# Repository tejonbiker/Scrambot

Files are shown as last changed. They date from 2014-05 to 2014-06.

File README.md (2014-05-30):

Scrambot
========

29/May/2014

University of Guanajuato

Division de Ingenierias Campus Irapuato Salamanca (DICIS)

Jose Federico Ramos Ortega

Scrambot is a differential mobile robot controlled via WiFi based
on a beetle robot from Steren as chassis and a Raspberry Pi as core of the controller.

This project begins with the ASME SPDC contest in 2013: "Remote Inspection Device":

https://www.asme.org/events/competitions/student-design-competition

The targets and the rules were quite simple:

    -The robot operator cannot see the stage
    -The robot need to establish (in any way) a real time video with the operator
    -The robot need to be controlled wirelessly
    -The robot need to accomplish three tasks:
      1.-Read a label with four numbers
      2.-Carry a small wood cylinder
      3.-Push a button 
          
The best balance between cost and flexibility was the Raspberry Pi with a lot of add-ons.
The result of the contest was this project (with a more little post work), this repo have the intention
to be a source of knowledge and contact that you require if you want to reconstruct/improve this project. 

Some topics/knowledge used in this robot are:

    -Remote connections
      -SSH
      -VNC
      -TCP sockets for server and client (ANSIC C and Java respectively)
      -MJPEG Server
      
    -Java Desktop GUI
      -Sockets
      -MJPEG Capture and show
      
    -PCB Design (with Eagle)
      -5V Switched Mode Power Suypply
      -Raspberry Pi GPIO and two L293 H-Bridge interface
      
    -Raspberry Pi GPIO management
      -WiringPi
      -I2C (for MPU6050 acelerometter)
      
    -Power Management 
      -Knowledge about batteries (NiCd - Lipo)
      -5V SMPS design
      -Power consumption analysis
      
    -Linux stuff
      -SSH and console commands management
      -Bash scripting
        -Automatically start services
        -Automatically install software
      -Make for compilation in ANSI C
      
    -Wireless LAN magagement
      -Detecting the Scrambot in LAN
      -Scrambot as hotspot
  
(Breathe.......) and much more.

For any misspelling/correction/comment/idea don't doubt to contact me.

tejonbiker@gmail.com

We will be happy if you like the project. 

Don't forget this is a MIT licensed project.

Have fun!!!!! :D

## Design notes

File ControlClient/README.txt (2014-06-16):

Scrambot Control Client

This is a desktop Java Application build on Netbeans, uses the GUI of the netbeans,
this means you only can compile with Netbeans.

The basics actions of the GUI are:
		-Open a socket connection to transfer control commands
		-Open a stream to capture the MJPEG from Scrambot
		-Capture the press/release keys 
		-Search the Scrambot in a range of IP

The application is entirely crossplatform, can be used (and develop) in any
OS that support Netbeans, currently I only tested in Linux/Win/Mac.

The executable is dist/ControlClient.jar

I highly recommend start with the file ControlGUI.java if you want inspect the code.

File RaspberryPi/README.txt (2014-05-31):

This folder includes all software related to the Raspbery Pi, as you can see the
is not much as you can think, the most large file is ScramConfig.sh
this script configures a Raspian OS to install all features of the Scrambot
and be recognized by GUI ControlClient.

The main problem is the MJPEG source, this code have some changes that need to be uptaed
in the script.

If you are in Windows please open or edit this files with CodeBlocks or some similar
IDE that recognizes Linux end lines, Visual Studio rewrites this to windows end lines.

server3.c uses WiringPi to acces to the Raspberry Pi GPIO, aditionally provides the service
(via sockets) that ControlClient uses to transfer the control commands, all is maded in ANSI C.

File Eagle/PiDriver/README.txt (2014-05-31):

PiDrive
This board designed to interface four motors with complete H-bridge, 
this task is accomplished with two L293 IC, some other sutff is addded,
like a PIC (MCU) to monitor the input voltage for the motors, the PIC is
not tested yet.

The board don't integrate a regulador to feed the Raspberry Pi with the
battery of the motors, this board only connect the battery for the motors.

The MPU6050 pinout works perfect.

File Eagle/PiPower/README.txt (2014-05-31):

PiPower
This board is designed to regulate 5V from 7V-15V battery
 voltage with an efficient  Switched Mode Power Supply, 
the board integrate an USB Female A conector to use a 
micro usb cable to power the pi, as is usual.

See more at datasheet of: LM2596

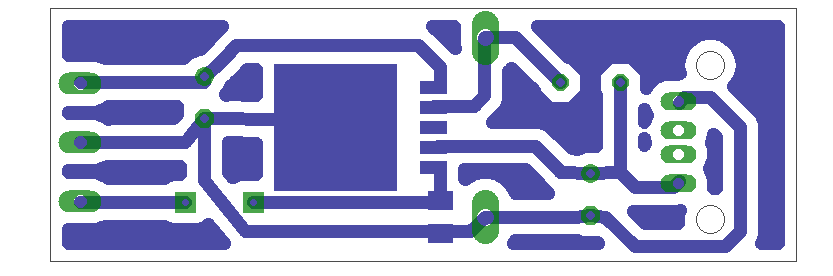
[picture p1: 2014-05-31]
Eagle/PiPower/PiPower_brd.png

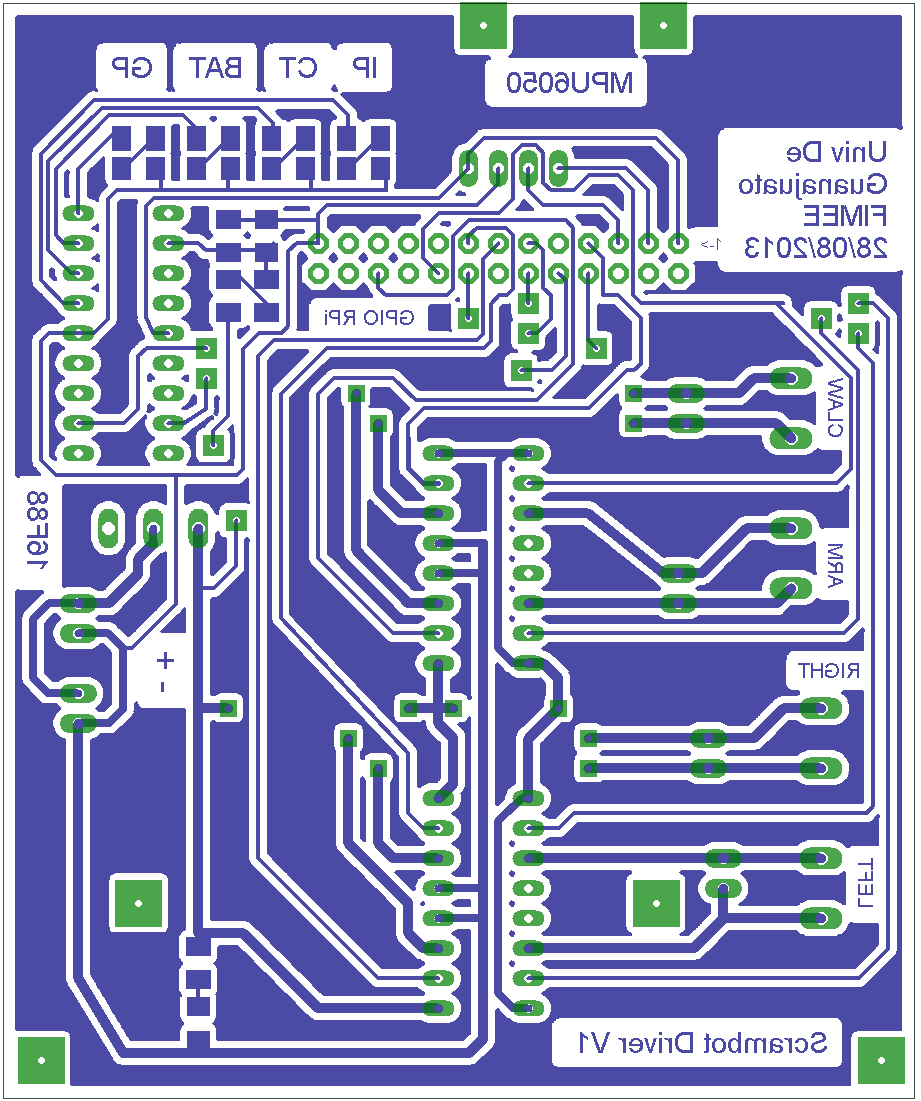
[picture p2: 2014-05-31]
Eagle/PiDriver/PiDrive_brd.png

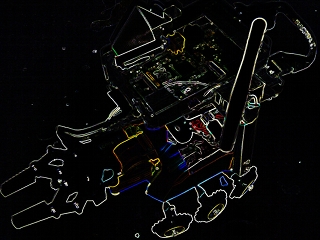
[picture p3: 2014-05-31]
ControlClient/src/blackscram.jpg

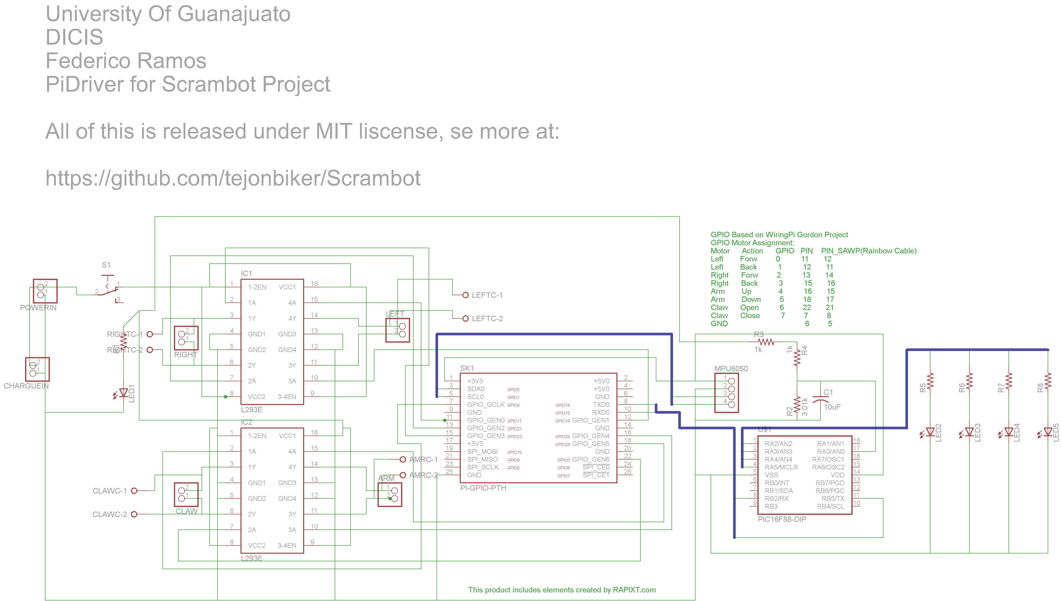
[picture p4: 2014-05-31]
Eagle/PiDriver/PiDriver_sch.png

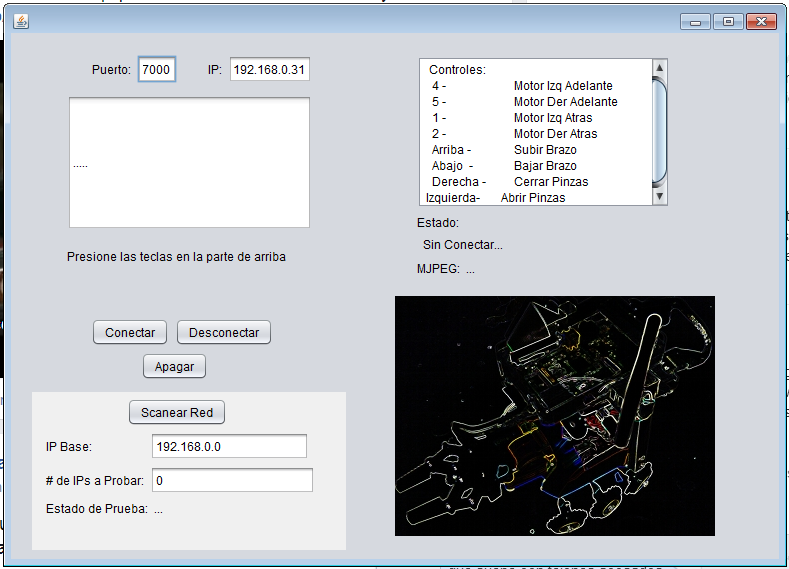
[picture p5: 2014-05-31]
ControlClient/capture_screen.png

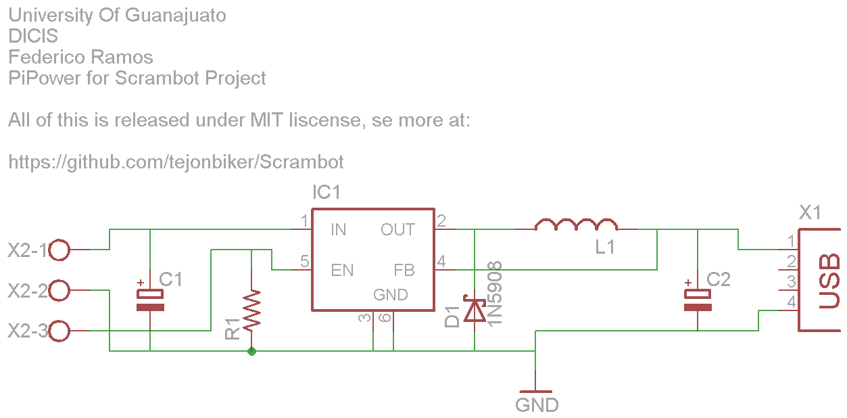
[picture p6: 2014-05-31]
Eagle/PiPower/PiPower_sch.png

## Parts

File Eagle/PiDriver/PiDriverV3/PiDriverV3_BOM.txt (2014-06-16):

Partlist exported from C:/GitHub/Scrambot/Eagle/PiDriver/PiDriverV3/PiDriverV3.sch at 08/06/2014 11:17:48 p.m.

Part      Value        Device       Package        Description                     MF                MPN   OC_FARNELL OC_NEWARK
AMRC                   W237-02P     W237-132       WAGO SREW CLAMP                                         unknown    unknown  
ARM                    PINHD-1X2    1X02           PIN HEADER                                                                  
C1        10uF         C-USC1206    C1206          CAPACITOR, American symbol                                                  
CHARGUEIN              PINHD-1X2    1X02           PIN HEADER                                                                  
CLAW                   PINHD-1X2    1X02           PIN HEADER                                                                  
CLAWC                  W237-02P     W237-132       WAGO SREW CLAMP                                         unknown    unknown  
D1        1N5819-T     1N5819-T     DO41-7.6       1.0A SCHOTTKY BARRIER RECTIFIER                                             
D2        1N5819-T     1N5819-T     DO41-7.6       1.0A SCHOTTKY BARRIER RECTIFIER                                             
D3        1N5819-T     1N5819-T     DO41-7.6       1.0A SCHOTTKY BARRIER RECTIFIER                                             
D4        1N5819-T     1N5819-T     DO41-7.6       1.0A SCHOTTKY BARRIER RECTIFIER                                             
D5        1N5819-T     1N5819-T     DO41-7.6       1.0A SCHOTTKY BARRIER RECTIFIER                                             
D6        1N5819-T     1N5819-T     DO41-7.6       1.0A SCHOTTKY BARRIER RECTIFIER                                             
D7        1N5819-T     1N5819-T     DO41-7.6       1.0A SCHOTTKY BARRIER RECTIFIER                                             
D8        1N5819-T     1N5819-T     DO41-7.6       1.0A SCHOTTKY BARRIER RECTIFIER                                             
D9        1N5819-T     1N5819-T     DO41-7.6       1.0A SCHOTTKY BARRIER RECTIFIER                                             
D10       1N5819-T     1N5819-T     DO41-7.6       1.0A SCHOTTKY BARRIER RECTIFIER                                             
D11       1N5819-T     1N5819-T     DO41-7.6       1.0A SCHOTTKY BARRIER RECTIFIER                                             
D12       1N5819-T     1N5819-T     DO41-7.6       1.0A SCHOTTKY BARRIER RECTIFIER                                             
D13       1N5819-T     1N5819-T     DO41-7.6       1.0A SCHOTTKY BARRIER RECTIFIER                                             
D14       1N5819-T     1N5819-T     DO41-7.6       1.0A SCHOTTKY BARRIER RECTIFIER                                             
D15       1N5819-T     1N5819-T     DO41-7.6       1.0A SCHOTTKY BARRIER RECTIFIER                                             
D16       1N5819-T     1N5819-T     DO41-7.6       1.0A SCHOTTKY BARRIER RECTIFIER                                             
IC1       L293E        L293E        DIL16          TI DEVICE                       Arrow Electronics L293E 1467711    89K0732  
IC2       L293E        L293E        DIL16          TI DEVICE                       Arrow Electronics L293E 1467711    89K0732  
LED1                   LEDSMT1206   1206           LED                                                                         
LED2                   LEDSMT1206   1206           LED                                                                         
LED3                   LEDSMT1206   1206           LED                                                                         
LED4                   LEDSMT1206   1206           LED                                                                         
LED5                   LEDSMT1206   1206           LED                                                                         
LEFT                   PINHD-1X2    1X02           PIN HEADER                                                                  
LEFTC                  W237-02P     W237-132       WAGO SREW CLAMP                                         unknown    unknown  
MPU6050                PINHD-1X4    1X04           PIN HEADER                                                                  
POWERIN                PINHD-1X2    1X02           PIN HEADER                                                                  
R1                     R-US_M1206   M1206          RESISTOR, American symbol                                                   
R2        3.01k        R-US_M1206   M1206          RESISTOR, American symbol                                                   
R3        1k           R-US_M1206   M1206          RESISTOR, American symbol                                                   
R4        1k           R-US_M1206   M1206          RESISTOR, American symbol                                                   
R5                     R-US_M1206   M1206          RESISTOR, American symbol                                                   
R6                     R-US_M1206   M1206          RESISTOR, American symbol                                                   
R7                     R-US_M1206   M1206          RESISTOR, American symbol                                                   
R8                     R-US_M1206   M1206          RESISTOR, American symbol                                                   
RIGHT                  PINHD-1X2    1X02           PIN HEADER                                                                  
RIGHTC                 W237-02P     W237-132       WAGO SREW CLAMP                                         unknown    unknown  
S1                     255SB        255SB          SLIDING SWITCH                                                              
SK1       PI-GPIO-PTH  PI-GPIO-PTH  GPIO-CONNECTOR Raspberry Pi                                                                
SMPS                   PINHD-1X2    1X02           PIN HEADER                                                                  
U$1       PIC16F88-DIP PIC16F88-DIP DIL18          8-bit PIC uC

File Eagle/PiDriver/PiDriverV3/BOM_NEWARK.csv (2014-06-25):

N.º de artículo | No. Parte Newark | ¿Conforme a RoHS? | Notas | Cantidad | Número Parte Fabricante | Fabricante / Descripción | Disponibilidad | Precio unitario | Total de línea | Precio de descuento
1 | 41K4141 | YES |  | 1.0 | LM2675M-5.0/NOPB | TEXAS INSTRUMENTS IC, STEP-DOWN REGULATOR, SOIC-8 TEXAS INSTRUMENTS-LM2675M-5.0/NOPB-IC, STEP-DOWN REGULATOR, SOIC-8 | 5500 | 5.97 | 5.97
2 | 68R4966 | YES |  | 2.0 | CC1206KRX7R9BB103 | YAGEO CAPACITOR CERAMIC 0.01UF, 50V, X7R, 10%, 1206 YAGEO-CC1206KRX7R9BB103-CAPACITOR CERAMIC 0.01UF, 50V, X7R, 10%, 1206 | 5460 | 0.05 | 0.10
3 | 46P8758 | YES |  | 1.0 | 13R473C | MURATA POWER SOLUTIONS INDUCTOR, 47UH, 1.5A, RADIAL LEADED MURATA POWER SOLUTIONS-13R473C-INDUCTOR, 47UH, 1.5A, RADIAL LEADED | 329 (Disponible hasta que se agoten las existencias) | 0.85 | 0.85
4 | 16M7370 | YES |  | 1.0 | EKZE160ELL680MF07D | UNITED CHEMI-CON CAPACITOR ALUM ELEC 68UF, 16V, 20%, RADIAL UNITED CHEMI-CON-EKZE160ELL680MF07D-CAPACITOR ALUM ELEC 68UF, 16V, 20%, RADIAL | 728 | 0.38 | 0.38
5 | 38K4678 | YES |  | 1.0 | MCGPR25V107M6.3X11 | MULTICOMP CAPACITOR ALUM ELEC 100UF, 25V, 20%, RADIAL MULTICOMP-MCGPR25V107M6.3X11-CAPACITOR ALUM ELEC 100UF, 25V, 20%, RADIAL | 3638 | 0.14 | 0.14
6 | 05R5876 | YES |  | 1.0 | SSA23L-E3/61T | VISHAY GENERAL SEMICONDUCTOR SCHOTTKY RECTIFIER, 2A 30V DO-214AC VISHAY GENERAL SEMICONDUCTOR-SSA23L-E3/61T-SCHOTTKY RECTIFIER, 2A 30V DO-214AC | 952 | 0.31 | 0.31
7 | 90R9531 | Y-EX |  | 16.0 | 1N5819 | MULTICOMP SCHOTTKY DIODE, 1A, 40V, DO-41 MULTICOMP-1N5819-SCHOTTKY DIODE, 1A, 40V, DO-41 | 5056 | 0.08 | 1.31
8 | 08F8145 | YES |  | 2.0 | SN754410NE | TEXAS INSTRUMENTS IC, PERIPHERAL DRIVER, HALF-H, 1A, DIP16 TEXAS INSTRUMENTS-SN754410NE-IC, PERIPHERAL DRIVER, HALF-H, 1A, DIP16 | 71 | 3.38 | 6.76
9 | 70R0063 | YES |  | 4.0 | PT1 | 5/2-5.0-H | PHOENIX CONTACT TERM BLOCK, PCB, SCREW, 5.0MM, 2WAY PHOENIX CONTACT-PT1,5/2-5.0-H-TERM BLOCK, PCB, SCREW, 5.0MM, 2WAY | 3468 | 0.50 | 1.98
10 | 54K2830 | YES |  | 1.0 | PIC16F88-I/P | MICROCHIP MCU, 8BIT, PIC16, 20MHZ, DIP-18 MICROCHIP-PIC16F88-I/P-MCU, 8BIT, PIC16, 20MHZ, DIP-18 | 1332 | 3.39 | 3.39
11 | 89M6854 | YES |  | 1.0 | CRCW12062K61FKEA | VISHAY DALE RESISTOR, THICK FILM, 2.61KOHM, 250mW, 1% VISHAY DALE-CRCW12062K61FKEA-RESISTOR, THICK FILM, 2.61KOHM, 250mW, 1% | 3571 | 0.14 | 0.14
12 | 53K2402 | Y-EX |  | 1.0 | CRCW1206422RFKEA | VISHAY DALE RESISTOR, THICK FILM, 422 OHM, 250mW, 1% VISHAY DALE-CRCW1206422RFKEA-RESISTOR, THICK FILM, 422 OHM, 250mW, 1% | 2743 | 0.01 | 0.01
13 | 75R5071 | YES |  | 1.0 | BZV55-C3V3 | 115 | NXP ZENER DIODE, 500mW, 3.3V, SOD-80C NXP-BZV55-C3V3,115-ZENER DIODE, 500mW, 3.3V, SOD-80C | 2368 | 0.03 | 0.03
14 | 70K9170 | YES |  | 1.0 | C1206C106K4RACTU | KEMET CAPACITOR CERAMIC, 10UF, 16V, X7R, 10%, 1206 KEMET-C1206C106K4RACTU-CAPACITOR CERAMIC, 10UF, 16V, X7R, 10%, 1206 | 2770 | 0.54 | 0.54
15 | 93K6506 | YES |  | 1.0 | CMD15-21VRD/TR8 | CHICAGO MINIATURE LIGHTING LED, RED, 1.5MM X 2MM, 4MCD, 640NM CHICAGO MINIATURE LIGHTING-CMD15-21VRD/TR8-LED, RED, 1.5MM X 2MM, 4MCD, 640NM | 3703 | 0.27 | 0.27
16 | 15M8857 | YES |  | 2.0 | CMD15-21VGC/TR8 | CHICAGO MINIATURE LIGHTING LED, GREEN, 1.5MM X 2MM, 10MCD, 570NM CHICAGO MINIATURE LIGHTING-CMD15-21VGC/TR8-LED, GREEN, 1.5MM X 2MM, 10MCD, 570NM | 2277 | 0.28 | 0.56
17 | 93K6508 | YES |  | 2.0 | CMD15-21VYD/TR8 | CHICAGO MINIATURE LIGHTING LED, YELLOW, 1.5MM X 2MM, 4MCD, 585NM CHICAGO MINIATURE LIGHTING-CMD15-21VYD/TR8-LED, YELLOW, 1.5MM X 2MM, 4MCD, 585NM | 962 | 0.27 | 0.54
18 | 79M6160 | YES |  | 1.0 | MC1206S4F2200T5E | MULTICOMP RESISTOR, THICK FILM, 220 OHM, 250mW, 1% MULTICOMP-MC1206S4F2200T5E-RESISTOR, THICK FILM, 220 OHM, 250mW, 1% | 1624 | 0.10 | 0.10
19 | 53K2345 | Y-EX |  | 1.0 | CRCW12064K02FKEA | VISHAY DALE RESISTOR, THICK FILM, 4.02KOHM, 250mW, 1% VISHAY DALE-CRCW12064K02FKEA-RESISTOR, THICK FILM, 4.02KOHM, 250mW, 1% | 4917 | 0.01 | 0.01
 |  |  |  |  |  |  | Subtotal | 23.40
 |  |  |  |  |  |  | Total de mercancías | 23.40
 |  |  |  |  |  |  | Envío básico | 0.00
 |  |  |  |  |  |  | Impuestos | 0.00
 |  |  |  |  |  |  | Total | 23.40

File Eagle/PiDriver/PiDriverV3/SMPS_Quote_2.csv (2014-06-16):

N.º de artículo | No. Parte Newark | ¿Conforme a RoHS? | Notas | Cantidad | Número Parte Fabricante | Fabricante / Descripción | Disponibilidad | Precio unitario | Total de línea | Precio de descuento
1 | 90W2861 | YES |  | 1.0 | MC0805B103J500CT | MULTICOMP CAP, MLCC, 10NF, 50V, X7R, 0805 MULTICOMP-MC0805B103J500CT-CAP, MLCC, 10NF, 50V, X7R, 0805 | 1569 | 0.11 | 0.11
2 | 41K4141 | YES |  | 1.0 | LM2675M-5.0/NOPB | TEXAS INSTRUMENTS IC, STEP-DOWN REGULATOR, SOIC-8 TEXAS INSTRUMENTS-LM2675M-5.0/NOPB-IC, STEP-DOWN REGULATOR, SOIC-8 | 6275 | 5.97 | 5.97
3 | 09J2996 | YES |  | 1.0 | SRU1048-470Y | BOURNS INDUCTOR, SHIELDED, 47UH, 1.5A, SMD BOURNS-SRU1048-470Y-INDUCTOR, SHIELDED, 47UH, 1.5A, SMD | Normalmente no está en inventario | 0.98 | 0.98
4 | 89K1595 | YES |  | 1.0 | STPS2150A | STMICROELECTRONICS SCHOTTKY RECTIFIER, 2A, 150V, DO-214AC STMICROELECTRONICS-STPS2150A-SCHOTTKY RECTIFIER, 2A, 150V, DO-214AC | 6639 | 0.79 | 0.79
 |  |  |  |  |  |  | Subtotal | 7.85
 |  |  |  |  |  |  | Total de mercancías | 7.85
 |  |  |  |  |  |  | Envío básico | 0.00
 |  |  |  |  |  |  | Impuestos | 0.00
 |  |  |  |  |  |  | Total | 7.85

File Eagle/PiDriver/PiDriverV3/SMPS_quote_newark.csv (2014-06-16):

N.º de artículo | No. Parte Newark | ¿Conforme a RoHS? | Notas | Cantidad | Número Parte Fabricante | Fabricante / Descripción | Disponibilidad | Precio unitario | Total de línea | Precio de descuento
1 | 04P2013 | YES |  | 3.0 | SRR1260-101M | BOURNS INDUCTOR, SHIELDED, 100UH, 1.7A, SMD BOURNS-SRR1260-101M-INDUCTOR, SHIELDED, 100UH, 1.7A, SMD | 634 | 1.31 | 3.93
2 | 53W3788 | YES |  | 6.0 | EEE-1EA101AP | PANASONIC CAPACITOR ALUM ELEC, 100UF, 25V, 20%, SMD PANASONIC-EEE-1EA101AP-CAPACITOR ALUM ELEC, 100UF, 25V, 20%, SMD | 960 | 0.70 | 4.18
3 | 65W8554 | YES |  | 3.0 | B240A-13-F | MULTICOMP DIODE, SCHOTTKY, 2A, 40V, DO-214AC-2 MULTICOMP-B240A-13-F-DIODE, SCHOTTKY, 2A, 40V, DO-214AC-2 | 1667 | 0.36 | 1.07
4 | 41K3690 | YES |  | 3.0 | LM2576S-5.0/NOPB | TEXAS INSTRUMENTS IC, STEP-DOWN VOLTAGE REGULATOR, TO-263 TEXAS INSTRUMENTS-LM2576S-5.0/NOPB-IC, STEP-DOWN VOLTAGE REGULATOR, TO-263 | 1480 | 4.42 | 13.26
 |  |  |  |  |  |  | Subtotal | 22.43
 |  |  |  |  |  |  | Total de mercancías | 22.43
 |  |  |  |  |  |  | Envío básico | 0.00
 |  |  |  |  |  |  | Impuestos | 0.00
 |  |  |  |  |  |  | Total | 22.43

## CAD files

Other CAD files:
media/ScrambotLogo.blend

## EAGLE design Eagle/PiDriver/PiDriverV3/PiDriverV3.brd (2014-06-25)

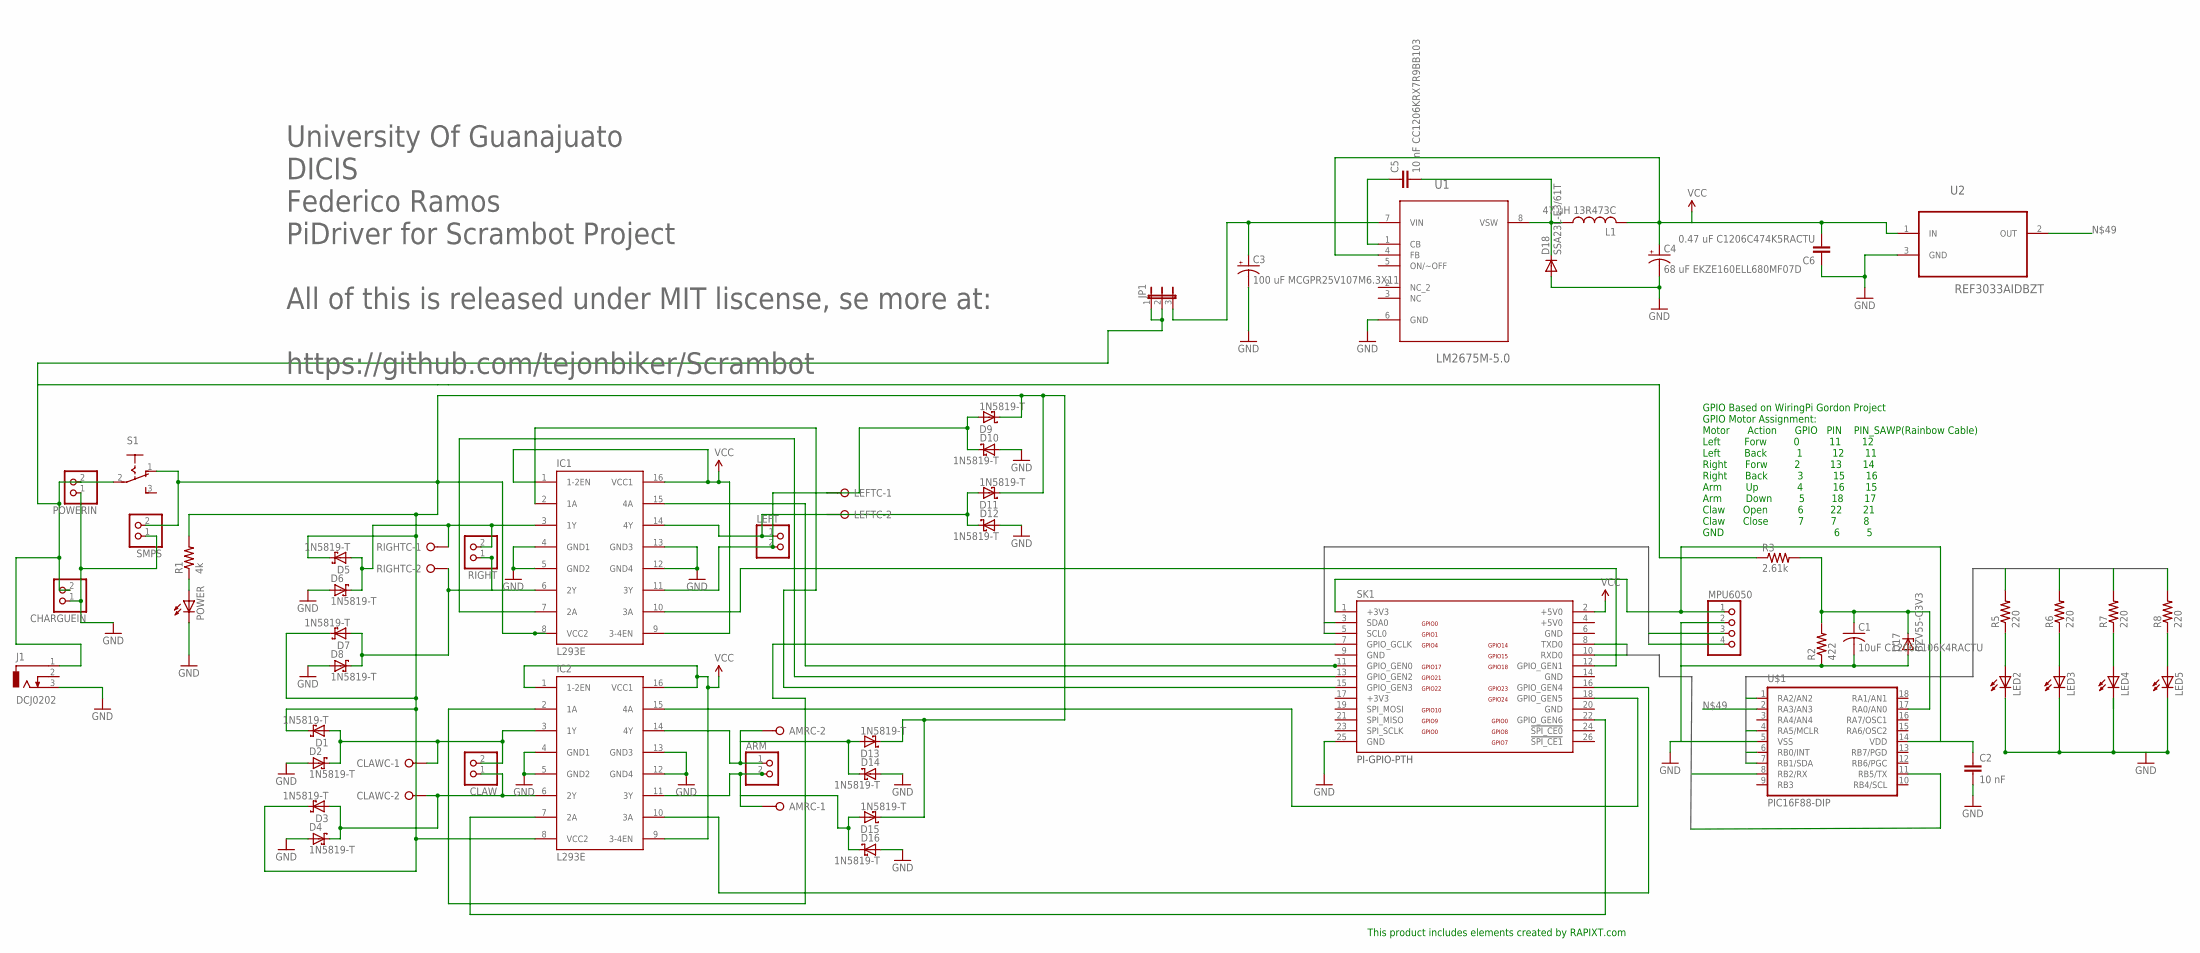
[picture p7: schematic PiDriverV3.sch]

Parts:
AMRC: W237-02P; W237-132
ARM: PINHD-1X2; 1X02
C1: 10uF C1206C106K4RACTU; C1206
C2: 10 nF; C1206
C3: 100 uF MCGPR25V107M6.3X11; E1,8-4
C4: 68 uF EKZE160ELL680MF07D; E1,8-4
C5: 10 nF CC1206KRX7R9BB103; C1206
C6: 0.47 uF C1206C474K5RACTU; C1206
CHARGUEIN: PINHD-1X2; 1X02
CLAW: PINHD-1X2; 1X02
CLAWC: W237-02P; W237-132
D1, D2, D3, D4, D5, D6, D7, D8, D9, D10, D11, D12, D13, D14, D15, D16: 1N5819-T; DO41-7.6
D17: BZV55-C3V3; SOD80C
D18: SSA23L-E3/61T; DO-214AC
IC1, IC2: L293E; DIL16
J1: DCJ0202
JP1: JP2E; JP2
L1: 47 uH 13R473C; 6000-XXXX-RC
LED2, LED3, LED4, LED5: LEDSMT1206; 1206
LEFT: PINHD-1X2; 1X02
LEFTC: W237-02P; W237-132
MPU6050: PINHD-1X4; 1X04
POWER: LEDSMT1206; 1206
POWERIN: PINHD-1X2; 1X02
R1: 4k; M1206
R2: 422; M1206
R3: 2.61k; M1206
R5, R6, R7, R8: 220; M1206
RIGHT: PINHD-1X2; 1X02
RIGHTC: W237-02P; W237-132
S1: 255SB
SK1: PI-GPIO-PTH; GPIO-CONNECTOR
SMPS: PINHD-1X2; 1X02
U1: LM2675M-5.0; SOIC127P620X175-8N
U2: REF3033AIDBZT; SOT95P237X112-3N
U$1: PIC16F88-DIP; DIL18

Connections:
+3V3: SK1.17 (+3V3)
+5V0: SK1.4 (+5V0)
ARMC: IC2.2 (1A), SK1.7 (GPIO_GCLK)
GND: C6.1, U2.3 (GND)
HTX: SK1.8 (TXD0), U$1.8 (RB2/RX)
unnamed: POWER.A, R1.1
unnamed: LED2.A, R5.1
unnamed: D9.A, D10.C, IC1.11 (3Y), LEFT.2, LEFTC.1
unnamed: IC2.10 (3A), SK1.16 (GPIO_GEN4)
unnamed: IC1.2 (1A), SK1.15 (GPIO_GEN3)
unnamed: IC1.7 (2A), SK1.13 (GPIO_GEN2)
unnamed: IC1.10 (3A), SK1.12 (GPIO_GEN1)
unnamed: D1.C, D3.C, D5.C, D7.C, D9.C, D11.C, D13.C, D15.C, IC1.8 (VCC2), IC2.8 (VCC2), R1.2, S1.1 (O), SMPS.2
unnamed: AMRC.2, ARM.1, D13.A, D14.C, IC2.14 (4Y)
unnamed: AMRC.1, ARM.2, D15.A, D16.C, IC2.11 (3Y)
unnamed: D11.A, D12.C, IC1.14 (4Y), LEFT.1, LEFTC.2
unnamed: R5.2, U$1.1 (RA2/AN2)
unnamed: C2.1, MPU6050.1, SK1.1 (+3V3), U$1.14 (VDD)
unnamed: IC2.15 (4A), SK1.18 (GPIO_GEN5)
unnamed: LED3.A, R6.1
unnamed: IC2.7 (2A), SK1.22 (GPIO_GEN6)
unnamed: SK1.10 (RXD0), U$1.11 (RB5/TX)
unnamed: CLAW.2, CLAWC.1, D1.A, D2.C, IC2.3 (1Y)
unnamed: D5.A, D6.C, IC1.3 (1Y), RIGHT.2, RIGHTC.1
unnamed: C5.2, D18.C, L1.1, U1.8 (VSW)
unnamed: IC1.15 (4A), SK1.11 (GPIO_GEN0)
unnamed: C3.+, JP1.3, U1.7 (VIN)
unnamed: C1.1, D17.C, R2.2, R3.2, U$1.17 (RA0/AN0)
unnamed: R6.2, U$1.4 (RA5/MCLR)
unnamed: LED4.A, R7.1
unnamed: CLAW.1, CLAWC.2, D3.A, D4.C, IC2.6 (2Y)
unnamed: D7.A, D8.C, IC1.6 (2Y), RIGHT.1, RIGHTC.2
unnamed: LED5.A, R8.1
unnamed: C5.1, U1.1 (CB)
unnamed: R7.2, U$1.6 (RB0/INT)
unnamed: C1.2, C2.2, C3.-, C4.-, CHARGUEIN.1, D2.A, D4.A, D6.A, D8.A, D10.A, D12.A, D14.A, D16.A, D17.A, D18.A, IC1.4 (GND1), IC1.5 (GND2), IC1.12 (GND4), IC1.13 (GND3), IC2.4 (GND1), IC2.5 (GND2), IC2.12 (GND4), IC2.13 (GND3), J1.3, LED2.C, LED3.C, LED4.C, LED5.C, MPU6050.2, POWER.C, POWERIN.1, R2.1, SK1.6 (GND), SK1.9 (GND), SK1.14 (GND), SK1.20 (GND), SK1.25 (GND), SMPS.1, U1.6 (GND), U$1.5 (VSS)
unnamed: R8.2, U$1.7 (RB1/SDA)
unnamed: U2.2 (OUT), U$1.2 (RA3/AN3)
unnamed: CHARGUEIN.2, J1.1, JP1.1, JP1.2, POWERIN.2, R3.1, S1.2
SCL: MPU6050.3, SK1.5 (SCL0)
SDA: MPU6050.4, SK1.3 (SDA0)
VCC: C4.+, C6.2, IC1.1 (1-2EN), IC1.9 (3-4EN), IC1.16 (VCC1), IC2.1 (1-2EN), IC2.9 (3-4EN), IC2.16 (VCC1), L1.2, SK1.2 (+5V0), U1.4 (FB), U2.1 (IN)

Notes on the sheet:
GPIO Based on WiringPi Gordon Project GPIO Motor Assignment: Motor Action GPIO PIN PIN_SAWP(Rainbow Cable) Left Forw 0 11 12 Left Back 1 12 11 Right Forw 2 13 14 Right Back 3 15 16 Arm Up 4 16 15 Arm Down 5 18 17 Claw Open 6 22 21 Claw Close 7 7 8 GND 6 5
This product includes elements created by RAPIXT.com
University Of Guanajuato DICIS Federico Ramos PiDriver for Scrambot Project All of this is released under MIT liscense, se more at: https://github.com/tejonbiker/Scrambot

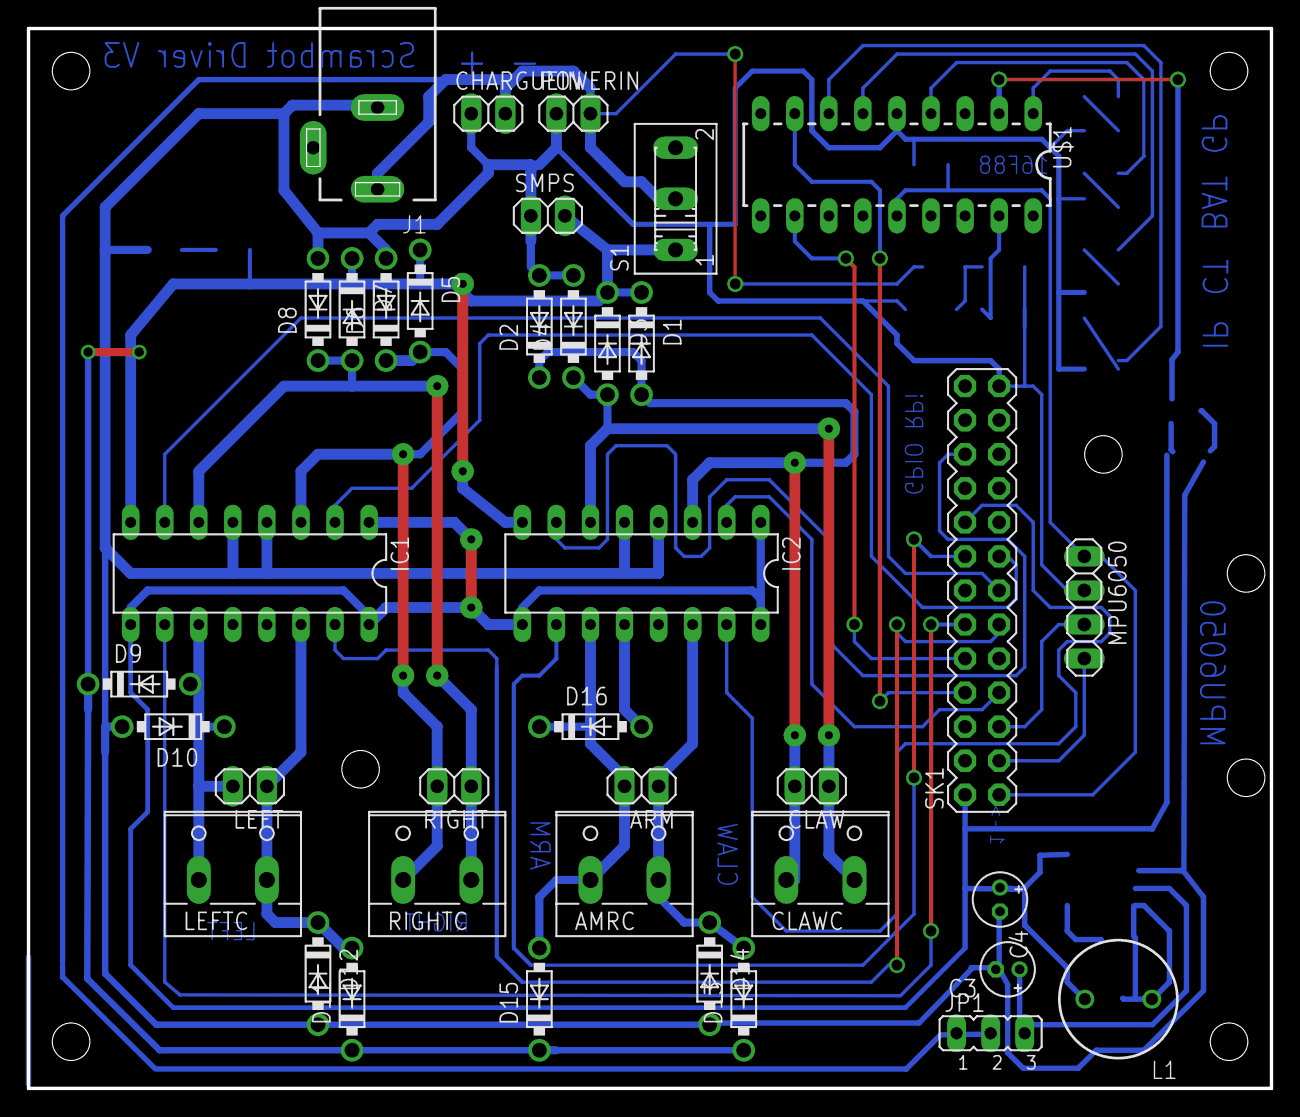
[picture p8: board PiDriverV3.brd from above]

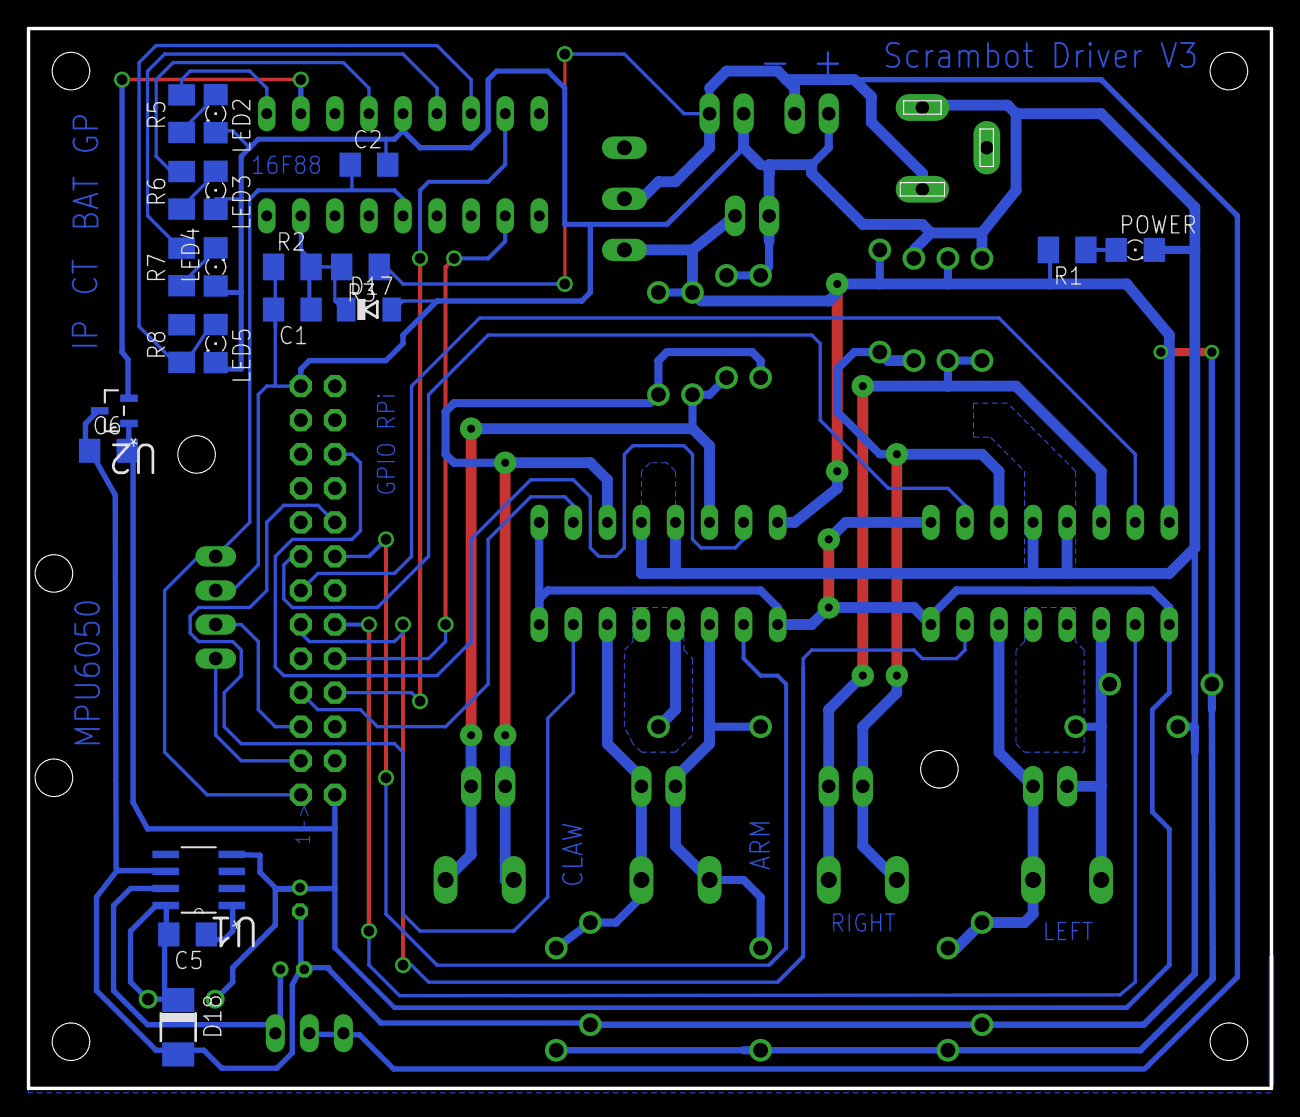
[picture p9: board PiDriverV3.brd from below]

Board: 2 copper layers, 92.7 x 79.0 mm, 58 parts (20 on the bottom side), 40 nets.

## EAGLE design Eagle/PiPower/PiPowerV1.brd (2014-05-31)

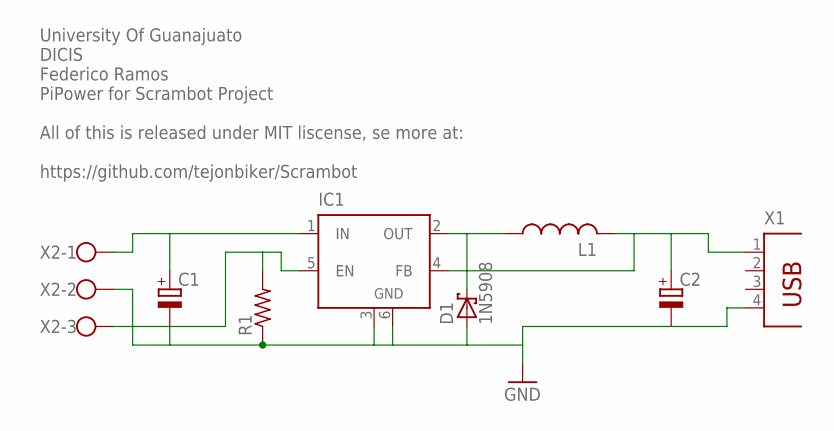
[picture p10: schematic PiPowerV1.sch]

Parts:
C1, C2: CPOL-EUE3.5-10; E3,5-10
D1: 1N5908; C4111-15
IC1: LM2596S; TO263-5
L1: L-US0204/5; 0204/5
R1: R-US_M1206; M1206
X1: PN87520
X2: W237-103

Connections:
unnamed: C2.+, IC1.4 (FB), L1.2, X1.1
unnamed: C1.+, IC1.1 (IN), X2.1
unnamed: IC1.5 (EN), R1.2, X2.3
unnamed: D1.C, IC1.2 (OUT), L1.1
unnamed: C1.-, C2.-, D1.A, IC1.3 (GND), IC1.6 (GND), R1.1, X1.4, X2.2

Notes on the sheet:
University Of Guanajuato DICIS Federico Ramos PiPower for Scrambot Project All of this is released under MIT liscense, se more at: https://github.com/tejonbiker/Scrambot

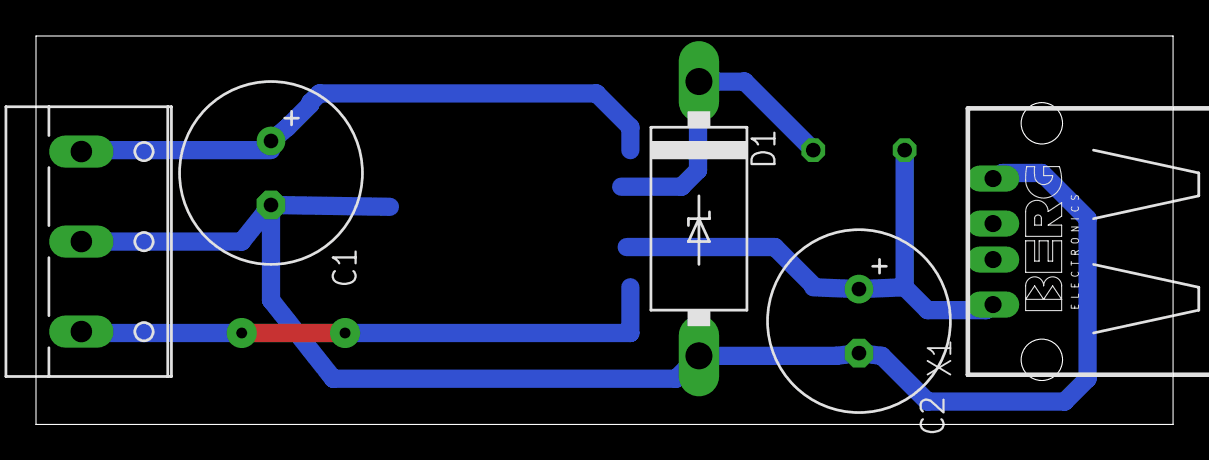
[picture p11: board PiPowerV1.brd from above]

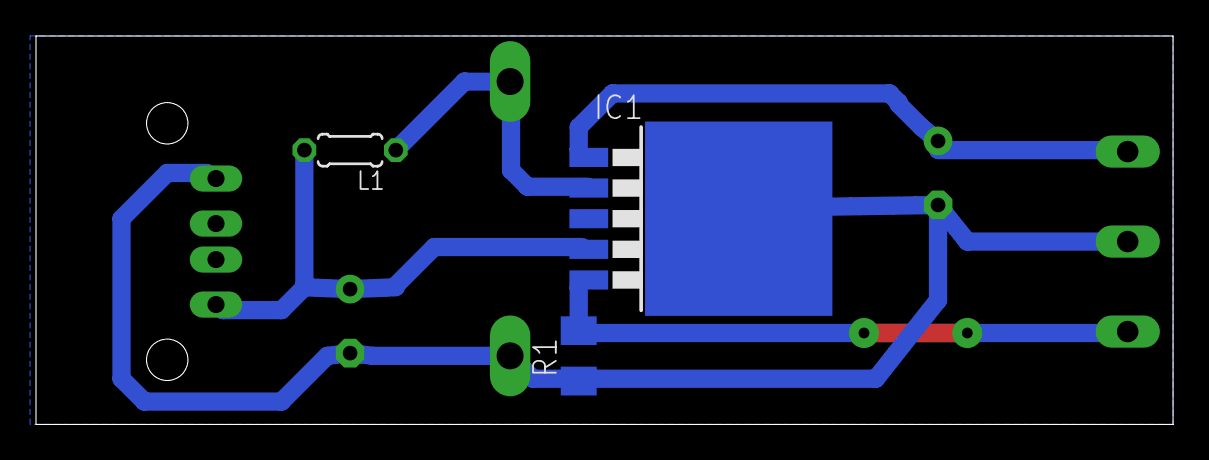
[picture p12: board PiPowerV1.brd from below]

Board: 2 copper layers, 63.2 x 21.6 mm, 8 parts (3 on the bottom side), 5 nets.

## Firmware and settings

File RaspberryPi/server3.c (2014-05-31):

/*
 * This software is part of the Scrambot project, for more info go to:
 * https://github.com/tejonbiker/Scrambot
 *
 * All source code of the project is MIT License
 *
 * This code is a modified version of:
 * http://www.linuxhowtos.org/C_C++/socket.htm
 *
 *
 * The workflow is as follow:
        Main:
                -Init WiringPi
                -Shutdown pins
                -Init Socket
                -Wait for a connection
        doStuff:
                -Send String ID
                -Read commands
                -put the commands to the GPIO
                -Wait for a command
 */

/* A simple server in the internet domain using TCP
 The port number is passed as an argument */


#include <stdio.h>
#include <stdlib.h>
#include <string.h>
#include <unistd.h>
#include <sys/types.h>
#include <sys/socket.h>
#include <netinet/in.h>

//For GPIO interface
#include <wiringPi.h>

//Flag that indicates we are in Raspberry Pi
//Added for some desktop Linux testings
#define RPI_SERVER

#define LED 0


//Debug output function
void error(const char *msg)
{
    perror(msg);
    exit(1);
}

//Function that children executes
void dostuff (int sock);

int main(int argc, char *argv[])
{
    //Paramters for socket connection
	int sockfd, newsockfd, portno;
	socklen_t clilen;
	int pid;
	char buffer[256];
	int i;
	struct sockaddr_in serv_addr, cli_addr;
	int n;

	//check for a port provided by user
	if (argc < 2) {
		fprintf(stderr,"ERROR, no port provided\n");
		exit(1);
	}

	printf("Ajustando GPIO...\n");

    //Setup WiringPi (and GPIOS)
	#ifdef RPI_SERVER
	//setup GPIO
	if(wiringPiSetup()==-1)
	{
		printf("Error al arrcancar WiringPi");
		return -2;
	}

    //Shutdown all pins, (for some reasen some pins boot)
    //with ones, until they are shutdown at this moment
	for(i=0;i<8;i++)
	{
		pinMode(i,OUTPUT);
		digitalWrite(i,0);
	}
	#endif

	printf("GPIO Listos\n");

    //let's begin with the sockets
	sockfd = socket(AF_INET, SOCK_STREAM, 0); //We want an internet socket
	if (sockfd < 0)
        error("ERROR opening socket");
	bzero((char *) &serv_addr, sizeof(serv_addr));


	portno = atoi(argv[1]);
	serv_addr.sin_family = AF_INET;         //We han a internet connection
	serv_addr.sin_addr.s_addr = INADDR_ANY;
	serv_addr.sin_port = htons(portno);     //Setup the port

	//Bind the socket to the parameters
	if (bind(sockfd, (struct sockaddr *) &serv_addr,
			 sizeof(serv_addr)) < 0)
		error("ERROR on binding");

    //only listen for 5 concurrently connections
	listen(sockfd,5);
	clilen = sizeof(cli_addr);

	while (1) {

		//Wair for a connection
		newsockfd = accept(sockfd, (struct sockaddr *) &cli_addr, &clilen);
		if (newsockfd < 0)
			error("ERROR on accept");
        //We duplicate the program, to avoid quit and kill the program
		pid = fork();
		if (pid < 0)
			error("ERROR on fork");
		if (pid == 0)  {
		    //the children excecutes the task (dostuff), the father wait for other
            //connections
			close(sockfd);
			dostuff(newsockfd);
			exit(0);
		}
		else close(newsockfd);
		printf("Cerrando Conexion\n");
	} /* end of while */
	close(sockfd);

	return 0;
}
/*For more info of how works this function see
    ControlGUI.java in ControlClient folder
*/
void dostuff (int sock)
{
	int n,m;
	char buffer[256];
	int i;

    //When a connection is stablished, the Scrambot send a string for ID
    //This is not a password!!!!
	n = write(sock,"TACOCABANA1989",14);
	n = write(sock,"1",1);

    //In reality this is an infinite loop
	while(n>0)
	{
	    //Wait for a command
		n = read(sock,buffer,255);
		//When a command is received, send a acknowledge
		m = write(sock,"OK",2);


		//Read the array and on the corresponding motor
		for(i=0;i<8;i++)
		{

			if(buffer[i]=='1')
			{
				#ifdef RPI_SERVER
				digitalWrite(i,1);
				#endif
			}
			else if(buffer[i]==216)
			{
			    //if the program send a special character in
			    //any slot, we shutdown the Raspberry Pi
			    printf("Apagando...");
			    system("sudo halt");
			    exit(0);
			}
			else
			{

				#ifdef RPI_SERVER
				digitalWrite(i,0);
				#endif
			}
		}

        //Clean un the buffer, to avoid fake readings
		buffer[8]=0;
	    //    printf("%s \n",buffer);
		//printf("%i\n",n);
	}

}

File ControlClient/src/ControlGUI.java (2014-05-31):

/*
 * This software is part of the Scrambot project, for more info go to:
 * https://github.com/tejonbiker/Scrambot
 * 
 * All source code of the project is MIT License
 * 
 * The workflow is as follow:
 *      ControlGUI()
 *          PiClient()
 *          MJPEGViewer()
 * 
 * From here the GUI events takes the control
 * 
 *      keypressed/keyReleased: control command user input (socket transfer via
 *                              PiClient)
 *      actionPerformed: Botton actions
 *              -Conectar: Open the sockets with the text on IP Jlabel,
 *                         Aditionaly init the MJPEG capture
 *              -Desconectar: close all connections
 *              -Apagar: Sends a special character to the server in
 *                       Scrambot that shutdown the Raspberry Pi
 *              -Scanear Red: Init the scanIPRange function
 * 
 *       scanIPRange: based on the values of the textbox "IP Base" and 
 *                  "# de IPs a Probar" scan a range of IP for the scrambot
 *                  and perform a full connection behavior if the scrambot
 *                  is found
 */
import java.awt.*;
import java.awt.event.ActionEvent;
import java.awt.event.ActionListener;
import java.awt.event.KeyEvent;
import java.awt.event.KeyListener;
import java.io.IOException;
import java.net.*;
import java.util.logging.Level;
import java.util.logging.Logger;
import javax.swing.*;

/*
 * To change this template, choose Tools | Templates
 * and open the template in the editor.
 */

/**
 *
 * @author Tejon
 */
public class ControlGUI extends javax.swing.JFrame implements KeyListener, ActionListener {

    /**
     * Creates new form ControlGUI
     */
    
    //Number of max transfered bytes in socket communication
    public static final int MAX_OUT_COMMANDS=8;
    public static final int MAX_IN_COMMANDS=8;
    
    //Buffer of the output/input bytes transfered by sockets
    char cmdOutArray[];
    char cmdInArray[];
    
    //For coloring the JLabel in GUI
    Color redColor;
    Color blackColor;
    
    //The Class that opens the socket for control commands
    PiClient client;
    
    //Required for MJPEGRunner to avoid lock the main
    //thread in the http petition of MJPEG stream
    Thread thread;
    
    //MJPEG Decoder
    MjpegRunner mjpeg_runner;
    
    //MJPEG GUI element
    MJPEGViewer mjpeg_viewer;
    
    //Classes to manage the repaint of the MJPEG GUI element
    JPanel JStream;
    RepaintManager myRepaintManager;
    
    //For Scrambot IP search in LAN
    Inet4Address current_addr;
    String IPBase;
    int    submask;
    int    IPToTest;
    String cutBase;
    
    //Image for showing in the MJPEG GUI element when the stream is closed
    Image blackScramImg;
    
    public ControlGUI()  {
        Component comp;
        int z;
        
        StringBuilder BuilderBaseIP= new StringBuilder();
        
        //Init all GUI components (by default)
        initComponents();
        
        //Add listeners (keys, buttons) to the apropiate controls
        BConect.addActionListener(this);
        BHalt.addActionListener(this);
        InputField.addKeyListener(this);
        ScanButton.addActionListener(this);
        BDisconnect.addActionListener(this);
        
        cmdOutArray =  new char[MAX_OUT_COMMANDS];
        cmdInArray  =  new char[MAX_IN_COMMANDS];
        client = new PiClient();
        
        //Setup some miscellaneous stuff
        StateLabel.setText("Sin Conectar...");
        StreamLabel.setText("...");
        
        for(int i=0;i<cmdOutArray.length ;i++)
        {
            cmdOutArray[i]='0';
        }
        
        redColor = new Color(255,0,0);
        blackColor= new Color(0,0,0);
        
        //Create the GUI element for MJPEG stream show
        mjpeg_viewer= new MJPEGViewer();
        
        //Load the stand-by element of the MJPEG stream show
        blackScramImg = new ImageIcon(getClass().getResource("/blackscram.jpg")).getImage();
        
        //Force dimentions and paint for the stand-by image
        mjpeg_viewer.setPreferredSize(new Dimension(320,240));
        mjpeg_viewer.setBackground(redColor);
        mjpeg_viewer.setImage(blackScramImg);
        mjpeg_viewer.revalidate();
        mjpeg_viewer.repaint();
        
        //We prefed IPV4, yes I know this is old, but is easy to manage
        System.setProperty("java.net.preferIPv4Stack","true");
        
        //Add the controller to the main grid layout
        comp =this.add(mjpeg_viewer); 
        
        /*  The scrambot have a little section that search the Scrambot IP in a range
            of IP, to help to the user we propose a base IP based in the IP of the
          * computer that run this App
        */
        try{
            
            //Get some data of local machine
            current_addr = (Inet4Address)Inet4Address.getLocalHost();
            IPBase = current_addr.getHostAddress();
            
            //This is only for emergencies, need more accurate code to identify IPv4
            InetAddress localHost = Inet4Address.getLocalHost();
            NetworkInterface networkInterface = NetworkInterface.getByInetAddress(localHost);
            System.out.println(networkInterface.getInterfaceAddresses().get(1).getNetworkPrefixLength());        
            submask=networkInterface.getInterfaceAddresses().get(1).getNetworkPrefixLength();
            
            //Try to propose the search range based on the network submask
            IPToTest=(int)Math.pow(2,32-submask);
            
            //Clean the string, I have this habit from ANSI C          
            BuilderBaseIP.delete(0, BuilderBaseIP.length());
            BuilderBaseIP.append(IPBase);
            BuilderBaseIP = BuilderBaseIP.reverse();
        
            //From the local current IP we delete the last number (remember we reversed
            //the string) finding the first point
            cutBase=BuilderBaseIP.substring(BuilderBaseIP.indexOf("."));
        
            BuilderBaseIP.delete(0, BuilderBaseIP.length());
            BuilderBaseIP.append(cutBase);
            BuilderBaseIP = BuilderBaseIP.reverse();
        
            //Finally we append a 0 to keep the a valid IP
            IPBase = BuilderBaseIP.toString() + "0";
        
            //for debuggin print out in the console the IP
             System.out.println(IPBase);
            
        }catch(UnknownHostException  e)
        {
            IPBase = "Net error";
            IPToTest=-1;
            
        }catch(SocketException e)
        {
            IPBase = "Net error";
            IPToTest=-1;
        }
        
        //print out in the GUI
        InputIPBase.setText(IPBase);
        InputBlockTest.setText(Integer.toString(IPToTest));
        StatusScan.setText("...");
        
    }
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

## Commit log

2014-05-31 Inital Release
    [PiDriverV2.brd, PiDriverV2.sch, PiPowerV1.brd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]
2014-06-08 PiDriver V3 was added, the V2 continues for reference, the new PCB now contain clamp diodes, that allow use L293B to feed four motor up to 1 A without damage
    [PiDriverV3.brd, PiDriverV3.sch, ScrambotLogo.blend]
2014-06-16 A second quote of smps for PiDrive was added
    [PiDriverV3.brd, PiDriverV3.sch, SMPS_Quote_2.csv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]
2014-06-18 An SMPS and Ref Voltage was added to PiDrive
    [PiDriverV3.brd, PiDriverV3.sch]
2014-06-25 some traces were fixed, the newark bom was added
    [BOM_NEWARK.csv, PiDriverV3.brd, PiDriverV3.sch]

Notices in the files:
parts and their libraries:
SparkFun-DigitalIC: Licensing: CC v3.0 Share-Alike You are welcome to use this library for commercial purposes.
